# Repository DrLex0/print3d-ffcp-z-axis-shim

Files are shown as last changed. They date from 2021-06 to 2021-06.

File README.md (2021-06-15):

# Z-Axis shim spacer for 2016 FlashForge Creator Pro (for glass bed, customizable)
*3D printable customizable shim for using a glass bed in the FlashForge Creator Pro 2016 and similar (formerly thing:1886458)*

### License
[Creative Commons - Attribution - Share Alike](https://creativecommons.org/licenses/by-sa/4.0/)

### Attribution
This is a remix of “Z-Axis Shim in 3mm/4mm/5mm Versions for Flashforge Creator Pro Variant Models Glass Bed Powerspec Pro” by Atomist ([Thingiverse thing:557994](https://www.thingiverse.com/thing:557994)), and “Z-Axis Shim for Flashforge Creator Pro (for glass bed sold by flashforge-eu.com)” by ben8p ([Thingiverse thing:1475239](https://www.thingiverse.com/thing:1475239)).

### Gallery

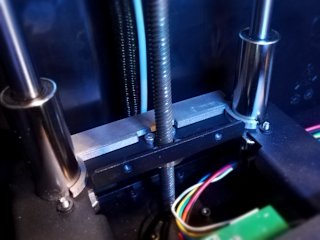
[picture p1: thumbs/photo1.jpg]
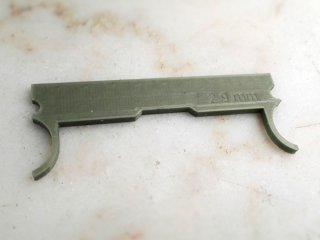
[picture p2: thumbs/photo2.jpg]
[🔎](images/photo1.jpg) [🔎](images/photo2.jpg)

## Description and Instructions

If you want to install a glass bed or another print surface of considerable thickness on your printer, you need to adjust the height at which the Z endstop is triggered, because the extra thickness of the glass is added to the platform. If you don't do this, the platform will level too high and you are likely to run out of adjustment length of the levelling springs and be unable to level the plate, or even risk ramming the nozzle into the glass and breaking it.

The easiest way to do this, is to add a *shim* to the rear of the platform at the location of the Z endstop, to raise this part with roughly the same amount as the thickness of the extra plate. There are many shims available but I couldn't find any for the 2016 FlashForge Creator Pro, which seems to have screws in different places than other models, so here's a remix that fits. Ready-to-use models are available in thicknesses from 2 to 6 mm (0.08 to 0.24 inch).

For those who want to make a custom shim of any thickness between 1 and 10 mm, a customizable OpenSCAD model is provided. Open the `.scad` file in [OpenSCAD](https://www.openscad.org/) and **[use the OpenSCAD Customizer](https://www.dr-lex.be/3d-printing/customizer.html)** to create a model with your own desired specifications.

The shims are designed to slightly clamp themselves between the rods, but if you print them in PLA and often do prints with a hot enclosed chamber, they may lose their ‘springiness’ over time and become a little wiggly. This is not a problem and does not affect their function.

### Hints for Printing

Print at 0.1 mm layers if you want a reasonably accurate thickness, although this would only matter if you regularly swap between glass plates and things of other thicknesses and don't want to have to make large readjustments each time.

Use proper cooling and a sufficient number of top layers to avoid ‘pillowing.’

I don't recommend ABS for the shim because flat objects like these tend to curl up a bit when the ABS cools down after being printed. It is best for the shim to be perfectly flat. PETG is a good material but PLA will also do fine unless you're really going to be printing in a very hot enclosed chamber.

## Updates

### 2016/11/12
First publication on Thingiverse.

### 2017/05/01
Added 6 mm version

### 2017/07/30
Added an option to Customizer to reinforce the center of the part around the hole for the Z axis leadscrew. This allows to make thin shims that do not bend easily.

### 2021/06/15
Migrated to GitHub.

## TAGS
`2016`, `bed_leveling`, `customizable`, `customizer`, `FFCP`, `FFCPRo`, `Glass_bed`, `shim`, `spacer`, `Z-Axis`

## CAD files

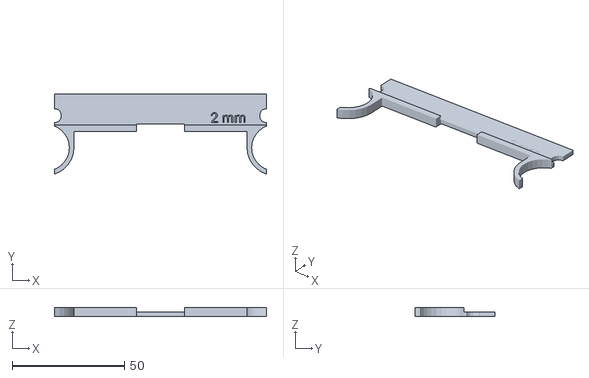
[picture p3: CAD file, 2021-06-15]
FFCP2016-shim-2mm.stl
94.5 x 35.8 x 4.00

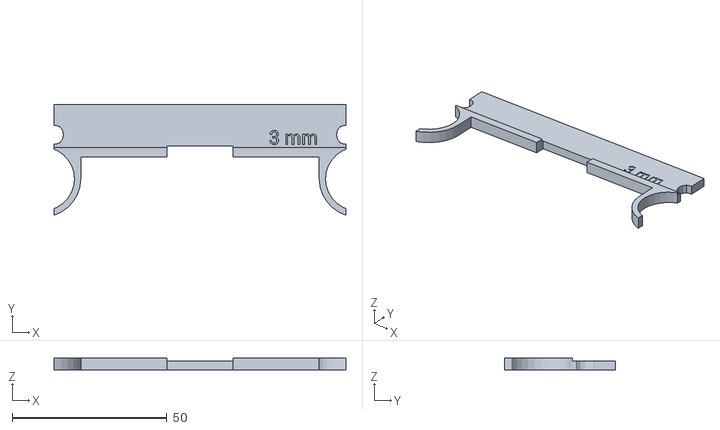
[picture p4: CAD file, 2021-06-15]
FFCP2016-shim-3mm.stl
94.5 x 35.8 x 4.00

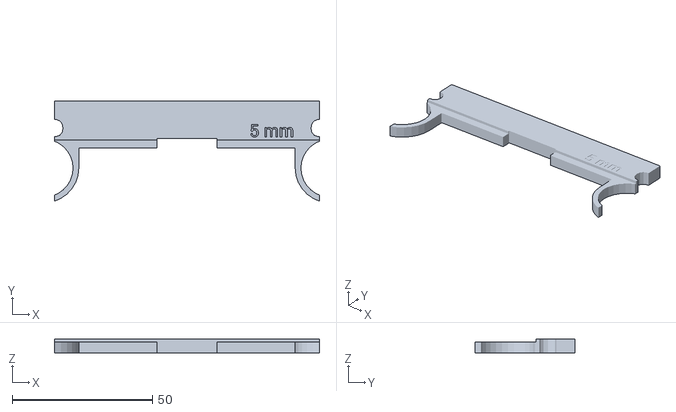
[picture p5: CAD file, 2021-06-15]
FFCP2016-shim-5mm.stl
94.5 x 35.8 x 5.00

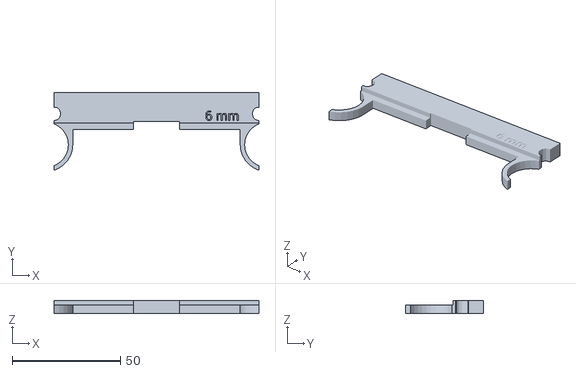
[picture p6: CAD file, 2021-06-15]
FFCP2016-shim-6mm.stl
94.5 x 35.8 x 6.00

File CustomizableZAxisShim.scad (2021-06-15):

// Customizable Z-axis shim for FlashForge Creator Pro 2016 by DrLex
// Based on Thing:1475239 by ben8p and Thing:557994 by Atomist
// Released under Creative Commons - Attribution - Share Alike license
// v2.1, 2019/08/10

// The distance you want the Z homing to be lowered.
ShimHeight = 3; // [1:0.1:10]
// How thick the clamping part should be.
ClampHeight = 4; // [2:0.1:10]
// Print the thickness on the model?
Label = "yes"; // [yes, no]
// Useful for very thin thims where Shimheight is smaller than ClampHeight.
Reinforce = "no"; // [yes, no]

/* [Hidden] */
RodDistance = 100; // [80:0.1:120]
RodDiameter = 19; // [15:0.1:25]

RodRadius = RodDiameter/2;
RodCenter = RodDistance/2 + 0.1;
MaxX = RodCenter - 2.85;
ClampScale = [1, 1.062, 1];

difference() {
    union() {
        difference() {
            union() {
                translate([-MaxX, 3, 0]) cube([2*MaxX, 13.88, ShimHeight]);
                translate([0, -2.0, ClampHeight/2]) cube([RodDistance, 10, ClampHeight], center=true);
                translate([RodCenter, -7.15, ClampHeight/2]) scale(ClampScale) cylinder(r=RodRadius + 2, h=ClampHeight, center=true, $fn=32);
                translate([-RodCenter, -7.15, ClampHeight/2]) scale(ClampScale) cylinder(r=RodRadius + 2, h=ClampHeight, center=true, $fn=32);
            }
            
            // Rod holes
            translate([RodCenter, -7.15, 9]) scale(ClampScale) cylinder(r=RodRadius, h=20, center=true, $fn=32);
            translate([-RodCenter, -7.15, 9]) scale(ClampScale) cylinder(r=RodRadius, h=20, center=true, $fn=32);
            
            // Side screw holes
            translate([MaxX, 7.155, 9]) cylinder(r=3.1, h=20, center=true);
            translate([-MaxX, 7.155, 9]) cylinder(r=3.1, h=20, center=true);

            
            // Chop off the sides
            translate([MaxX, -2*RodDiameter, -5]) cube([RodDiameter, 4 * RodDiameter, 20]);
            translate([-MaxX - RodDiameter, -2*RodDiameter, -5]) cube([RodDiameter, 4 * RodDiameter, 20]);
            // Chop off the center
            translate([0, -10, 9]) cube([2*(RodCenter - RodRadius - 2), 20, 20], center=true);
            
            if(ClampHeight > ShimHeight) {
                // Remove pieces of the clamps sticking out
                translate([-MaxX - 1, 3, ShimHeight]) cube([2*MaxX + 2, 13.88, 20]);
            }
        }

        if(Reinforce == "yes") {
            translate([0, 1.85, ClampHeight/2]) isoTrapezoidX(22, 30, 3.7, ClampHeight);
        }
    }
    
    // Space for leadscrew bearing
    if(Reinforce == "yes") {
        translate([0, 0, ClampHeight/2]) isoTrapezoidX(18, 28, 5, ClampHeight+0.1);
    }
    else {
        translate([0, 0, 9]) cube([21.35, 7, 20], center=true);
    }
        
    if(Label == "yes") {
        translate([MaxX-9, 4, ShimHeight - 0.2]) linear_extrude(1, convexity=3)  text(str(ShimHeight, " mm"), 4.5, font="Roboto", halign="right", $fn=14);
    }
}

module isoTrapezoidX(sizeXTop, sizeXBtm, sizeY, sizeZ) {
    linear_extrude(height=sizeZ, center=true) polygon([[-sizeXTop/2, sizeY/2], [sizeXTop/2, sizeY/2], [sizeXBtm/2, -sizeY/2], [-sizeXBtm/2, -sizeY/2]]);

}

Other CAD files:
FFCP2016-shim-4mm.stl
